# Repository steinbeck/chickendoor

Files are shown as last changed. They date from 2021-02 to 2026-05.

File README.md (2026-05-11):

# IoT Chicken Door

## Warning
This repo is here for documentation purposes only. I have retired this Chicken Door control in early 2026 and moved to a Shelly shutter control with a Shelly Plus 2PM and some relays. The software in this repo worked for many years, but was unreliable. I guess I put too much in it (lux sensor, temp, many timers). The Shelly solution is so much more reliable. :)

## Introduction
This is code for an ESP32-based Internet-of-Things (IoT) chicken door. We have a [Heini Koop chicken coop](https://www.heinicoop.de/produkt/heinicoop-huehnerstall-uno/), but the principle of this door mechanism is generic and should work with sliding and other doors.

Heini Koop Uno 
(c) Heini Koop. Picture from [Heini Koop Website](https://www.heinicoop.de/produkt/heinicoop-huehnerstall-uno/)

The ESP is hooked up to a BME280 climate sensor (not needed, just for fun) as well as a BH1750 light sensor, as well as a DC motordriver connected to a 30 cm DC actuator to open and close the door. We currently have a [ChickenGuard(TM)](https://www.chickenguard.de/) module to close and open the door. It works well, but lacks the Internet access. If you do not need the IoT functionality and do not want to tinker, go for the ChickenGuard(TM).
If, say, you are away from home and decide that you want to let the chicken out manually tomorrow, but the door is in lux-mode (opens when a certain amount of daylight is reached) then you need to live with the situation. 
Furthermore, if you discover on your coop camera :) that one of the chicken didn't get in before the door closed automatically in the evening and you are not at home, you cannot open the door remotely to let the late-comer in. In our rural area, the likelihood is high that you then have one saturated predator more in the area and one chicken less. 
Last but not least, the standard ChickenGuard (TM) door can be simply pushed up once closed. They do have a model that locks, though, but we have the standard model. The DC actuator keeps the door closed once it is closed. No way to push it up. The downside of the actuator is that it is very powerful. If something gets in the way when the door closes, it or the door gets damaged. 

Ok, so much for the motivation for this project. Here are the specs:

## Specifications

* 3 modes (manual-, time-based, light-based operation), independently selectable for opening and closing (e.g. open every morning at 8am, but close at night when the light is low).
* This obviously requires a light sensor. This one has a BH1750. You can also set a delay. If the light has been below or above threshold for a certain number of minutes, the door moves. 
* BME280 for temperature, humidity and pressure
* Manual opening and closing with two buttons at the device. 
* A INA219 current sensor that notices when the built-in end stops of the actuator have switched the device off, so the system knows when the door is fully open or closed. 
* Web interface for the settings and sensor readings.
* Linear actuator with 30 cm range of operation, IP66 approved for outdoor application. 

## Software
More todo here

Turns out that the ESP32 dev module can be picky with regard to which pins you can use for what. I tried around a bit and the following pins work for me:

* SDA 16
* SCL 17
* Motor_Pin_1 18
* Motor_Pin_2 19
* Button_1 26
* Button_2 27

## Web interface
I decided to build this device without a display and without the possiblity to adjust the settings directly at the device, apart from the two buttons to open and close the door. 
Instead, I added a web interface with a dashboard with two virtual buttons to open and close the door as well as some status information and sensor readings. 

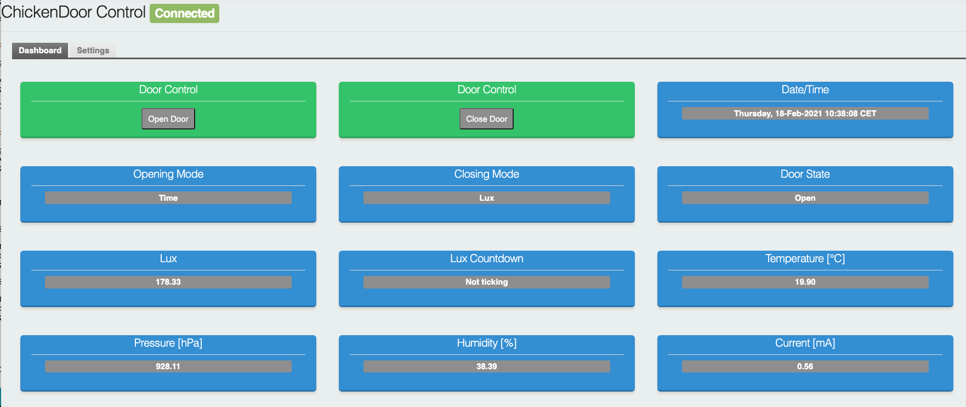
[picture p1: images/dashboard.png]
dashboard


And there is a settings panel. 

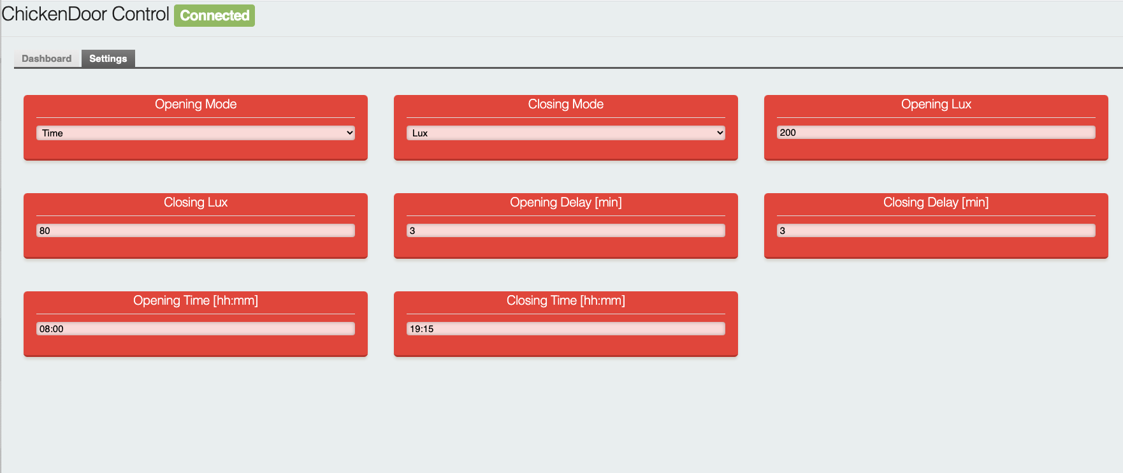
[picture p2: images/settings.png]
settings


## Development

The mechanism was first setup on a piece of plywood so I could carry it around and test and develop wherever I wanted:

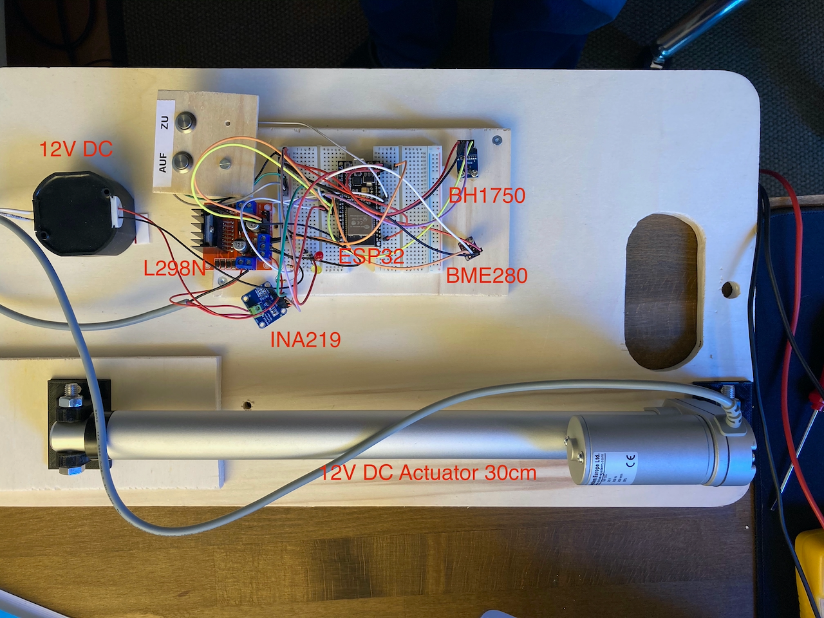
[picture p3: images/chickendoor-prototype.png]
Breadboard prototype of chicken door mechanism


Here is the fritzing schema (yes, I am sure this can be done nicer :)):

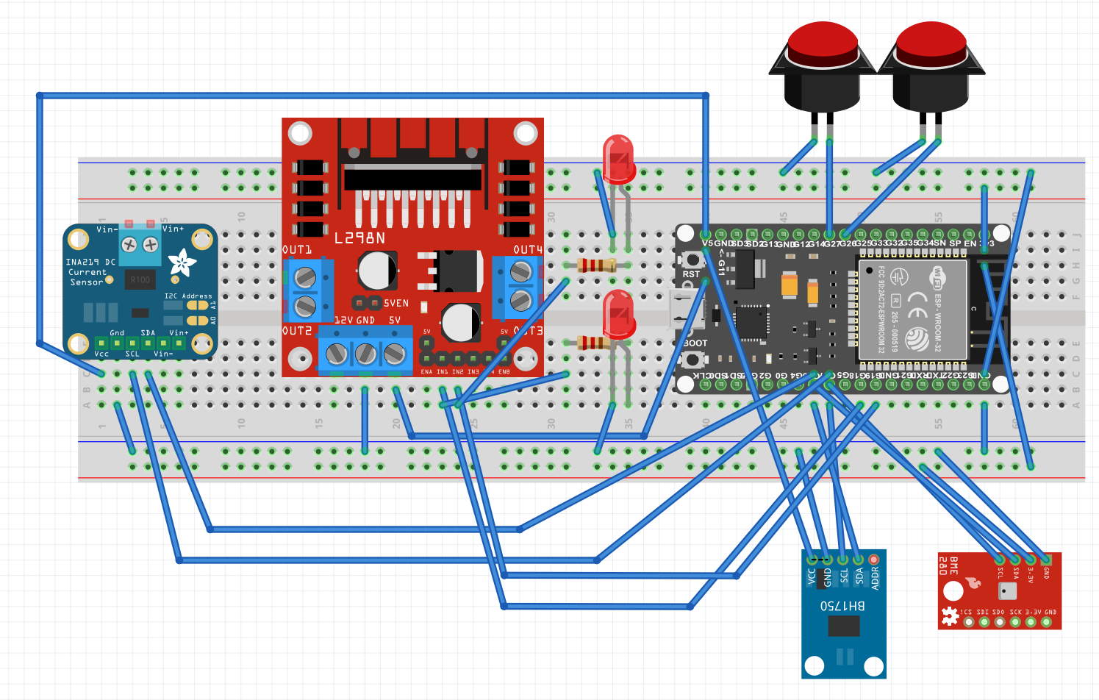
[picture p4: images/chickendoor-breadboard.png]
Breadboard prototype of chicken door mechanism


The mounts that came with the actuator where useless as too short to mount the actuator for vertical operation, so I designed a [mount in OpenSCAD](https://github.com/steinbeck/chickendoor/blob/main/actuator_mount.scad) and 3D printed it on my ender3. I eventually ordered the part in PA2020 (Nylon), 3D printed with Selective Laser Sintering (SLS), from [RapidObject GMBH](https://www.rapidobject.com/) in Germany for maximum strength and durability.

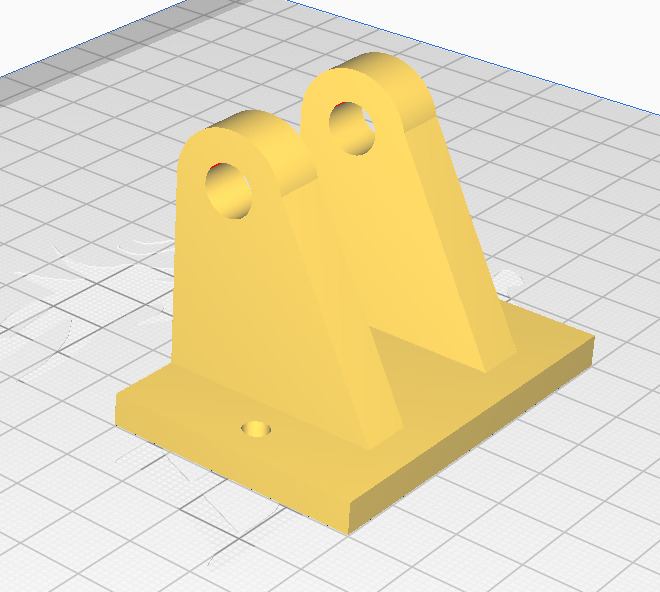
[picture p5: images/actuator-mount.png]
3D model of actuator mount


And here is the final assembly working and in action:

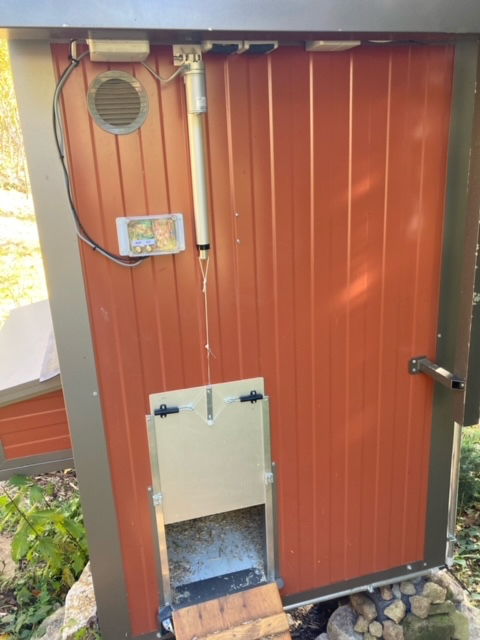
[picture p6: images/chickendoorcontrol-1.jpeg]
The whole assembly in action

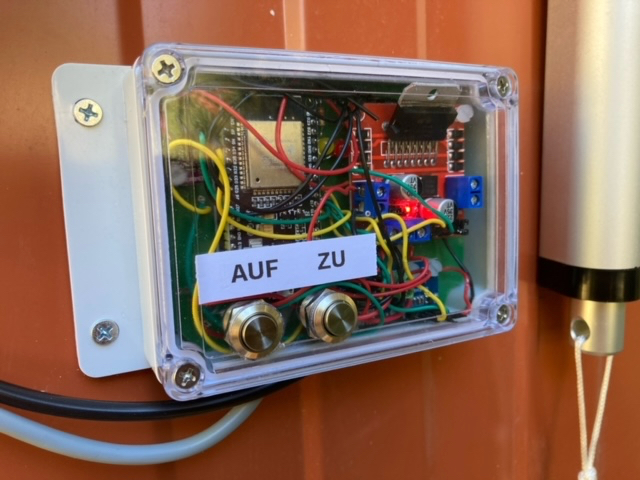
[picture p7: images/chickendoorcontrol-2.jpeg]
Close-up of control


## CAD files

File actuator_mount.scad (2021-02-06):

extrusion_length = 35;
hole_distance = 25;  // the distance of the mounting hole to the wall

mounting_plate_thickness = 5;
mounting_plate_height = 40;
mounting_plate_width = 60;
wall_screw_radius = 2;
m_screw_radius = 4; // The radius of the mounting hole in the actuator
extrusion_width = 5;
gap_width= 20;
wall_thickness = 5;
mount_wall_thickness = 8;
extrusion_height = (m_screw_radius + wall_thickness)*2;
extrusion_translation = mounting_plate_width /2 - gap_width / 2 - wall_thickness;

    union(){
        translate([0,mounting_plate_height - extrusion_height,extrusion_translation])
        {
            extrusion();
        }
        translate([0,mounting_plate_height - extrusion_height, mounting_plate_width - extrusion_translation - mount_wall_thickness])
        {
            extrusion();
        }

        mounting_plate();
    }
/*
* The part that extrudes from the mounting plate and 
*
*/
module extrusion()
{
       difference(){
            
            union()
            {    
                cube([extrusion_length, (m_screw_radius + mount_wall_thickness)*2, extrusion_width]);    
                translate([extrusion_length,extrusion_height/2,extrusion_width/2])
                {
                    cylinder(extrusion_width, m_screw_radius + wall_thickness, m_screw_radius + wall_thickness, true, $fn=1000);
                }
            }
            translate([extrusion_length, extrusion_height/2, extrusion_width/2 - 1])
            {
                cylinder(extrusion_width * 2, m_screw_radius, m_screw_radius, true, $fn=1000);
            }
        }
        translate([0, -extrusion_height - wall_thickness + 4, extrusion_width])
        {
            rotate([0,90,0])
            {
                prism(extrusion_width, mounting_plate_height - extrusion_height - 2, extrusion_length * 1.1);
            }
        }

}

module mounting_plate()
{
  
difference()
  {  
    cube([mounting_plate_thickness, mounting_plate_height, mounting_plate_width]);  
  
    translate([1, mounting_plate_height/2, mounting_plate_width*.15])
    {
            rotate([0,90,0])
            {
                wall_screw_hole();
            }
     }

    translate([1, mounting_plate_height/2, mounting_plate_width*.85])
    {
            rotate([0,90,0])
            {
                wall_screw_hole();
            }
     }
 }
}


module wall_screw_hole()
{
            cylinder(mounting_plate_thickness * 2 ,wall_screw_radius, wall_screw_radius, true, $fn=1000);
}

module prism(l, w, h){
   polyhedron(
           points=[[0,0,0], [l,0,0], [l,w,0], [0,w,0], [0,w,h], [l,w,h]],
           faces=[[0,1,2,3],[5,4,3,2],[0,4,5,1],[0,3,4],[5,2,1]]
           );
   
}

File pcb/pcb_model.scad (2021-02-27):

pcb_width = 107;
pcb_height = 77;
pcb_thickness = 1;
edge_cutout_radius = 6;
mount_hole_radius = 1.5;
mount_hole_distance_x = 78;
mount_hole_distance_y = 51;
bh1750_mount_hole_distance = 8.7;
bh1750_height = 20;
ina219_mount_hole_distance_x = 20;
ina219_mount_hole_distance_y = 17;
motor_driver_mount_hole_distance = 37;

projection() pcb();

module pcb()
{
    difference()
    {
        cube([pcb_width, pcb_height, pcb_thickness]);  
        translate([0,0,-.5])
        {
            edge_cutout();
        }
        translate([0,pcb_height,-.5])
        {
            edge_cutout();
        }
        translate([pcb_width,0,-.5])
        {
            edge_cutout();
        }
        translate([pcb_width,pcb_height,-.5])
        {
            edge_cutout();
        }

        // The four holes to mount the PCB to the case
        translate([(pcb_width - mount_hole_distance_x)/2, (pcb_height - mount_hole_distance_y)/2,-.5])
        {
            mount_hole();
        }
        translate([pcb_width-(pcb_width - mount_hole_distance_x)/2, (pcb_height - mount_hole_distance_y)/2,-.5])
        {
            mount_hole();
        }
        translate([(pcb_width - mount_hole_distance_x)/2, pcb_height - (pcb_height - mount_hole_distance_y)/2,-.5])
        {
            mount_hole();
        }
        translate([pcb_width-(pcb_width - mount_hole_distance_x)/2, pcb_height - (pcb_height - mount_hole_distance_y)/2,-.5])
        {
            mount_hole();
        }    
        
        // The two mount holes for the BH1750 light sensor
        
        translate([(pcb_width - mount_hole_distance_x)/2 - bh1750_mount_hole_distance, (pcb_height - mount_hole_distance_y)/2 +  10,-.5])
        {
            mount_hole();
        }
        translate([(pcb_width - mount_hole_distance_x)/2, (pcb_height - mount_hole_distance_y)/2 + 10,-.5])
        {
            mount_hole();
        }
        
        // The single mount hole for the BME208
        translate([(pcb_width - mount_hole_distance_x)/2 - bh1750_mount_hole_distance, (pcb_height - mount_hole_distance_y)/2 +  10 + bh1750_height + 5,-.5])
        {
            mount_hole();
        }
        
        // Four holes for the INA219 Current Sensor
        translate([pcb_width/2 + 5, 3,-.5])
        {
            mount_hole();
        }
        translate([pcb_width/2 + 5 + ina219_mount_hole_distance_x, 3,-.5])
        {
            mount_hole();
        }
        translate([pcb_width/2 + 5, 3 + ina219_mount_hole_distance_y,-.5])
        {
            mount_hole();
        }
        translate([pcb_width/2 + 5 + ina219_mount_hole_distance_x, 3 + ina219_mount_hole_distance_y,-.5])
        {
            mount_hole();
        }

        // three holes for the motor driver
        translate([pcb_width-(pcb_width - mount_hole_distance_x)/2 - motor_driver_mount_hole_distance, pcb_height - (pcb_height - mount_hole_distance_y)/2,-.5])
        {
            mount_hole();
        }    
        translate([pcb_width-(pcb_width - mount_hole_distance_x)/2 - motor_driver_mount_hole_distance, pcb_height - (pcb_height - mount_hole_distance_y)/2 - motor_driver_mount_hole_distance,-.5])
        {
            mount_hole();
        }    

        translate([pcb_width-(pcb_width - mount_hole_distance_x)/2, pcb_height - (pcb_height - mount_hole_distance_y)/2 - motor_driver_mount_hole_distance,-.5])
        {
            mount_hole();
        }    

        
    }
}

module edge_cutout()
{
    cylinder(pcb_thickness + 1, edge_cutout_radius,  edge_cutout_radius, $fn=1000);   
}

module mount_hole()
{
    cylinder(pcb_thickness + 1, mount_hole_radius, mount_hole_radius, $fn=1000);
}

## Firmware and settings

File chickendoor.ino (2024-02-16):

#include <Wire.h>
#include <BH1750.h>
#include <BME280I2C.h>
#include <WiFi.h>
#include <ezTime.h>
#include <Ticker.h>
#include <Preferences.h>
#include <Adafruit_INA219.h>

#include <AsyncEventSource.h>
#include <AsyncJson.h>
#include <SPIFFSEditor.h>
#include <WebHandlerImpl.h>
#include <ESPAsyncWebServer.h>
#include <AsyncElegantOTA.h>
#include <WebAuthentication.h>
#include <AsyncWebSynchronization.h>
#include <AsyncWebSocket.h>
#include <WebResponseImpl.h>
#include <StringArray.h>

#include <AsyncTCP.h>

#include <DNSServer.h>
#include <ESPUI.h>
#include <Update.h>
#include <PubSubClient.h>
#include <esp_task_wdt.h>
// logging to google sheets
#include <ESP_Google_Sheet_Client.h>

// MQTT library for home assistant
#include <ArduinoHA.h>


//10 seconds WDT ; Less screws up OTA
#define WDT_TIMEOUT 10
#define WL_MAC_ADDR_LENGTH 6


const byte DNS_PORT = 53;
IPAddress apIP(192, 168, 1, 1);
DNSServer dnsServer;

#if defined(ESP32)
#include <WiFi.h>
#else
#include <ESP8266WiFi.h>
#endif

//OTA with ESPUI solution thanks to user ENWI (https://githubmemory.com/repo/s00500/ESPUI/issues/116)
const char* OTA_INDEX PROGMEM
  = R"=====(<!DOCTYPE html><html><head><meta charset=utf-8><title>OTA</title></head><body><div class="upload"><form method="POST" action="/ota" enctype="multipart/form-data"><input type="file" name="data" /><input type="submit" name="upload" value="Upload" title="Upload Files"></form></div></body></html>)=====";

#include "secrets.h"

#define DOOR_UNDEFINED 0
#define DOOR_OPEN 1
#define DOOR_CLOSED 2
#define OP_MODE_MANUAL 0
#define OP_MODE_LUX 1
#define OP_MODE_TIME 2

Adafruit_INA219 ina219;
const char ssid[] = WIFI_SSID;
const char password[] = WIFI_PASSWD;
const char titleVersion[] = "Chicken Door Control V1.3.0";

WiFiClient client;
HADevice hadevice;
HAMqtt mqtt(client, hadevice);
//HASensor chickendoor("chickendoor");
HACover chickendoor("chickendoor", HACover::DefaultFeatures);

HASensorNumber volierelux("volierelux", HASensorNumber::PrecisionP1);
HASensor hadoorstate("doorstate");


// Service Account's private key
const char PRIVATE_KEY[] PROGMEM = PRIVATE_KEY_DEF;

// The ID of the spreadsheet where you'll publish the data
const char spreadsheetId[] = SPREADSHEET_ID;


// Token Callback function
void tokenStatusCallback(TokenInfo info);

//End of google sheet api config


Timezone myTZ;
BH1750 lightMeter;
BME280I2C bme;
unsigned int doorState = DOOR_UNDEFINED; // 1 is open, 2 is closed, use the defines above.
int motorPinForward = 18;
int motorPinBackward = 19;
int motorRunningSeconds = 0;
int motorRunDuration = 60;
boolean motorRunning = false;
int doorCylclingState = 0;
int networkUnreachableCount = 0;

int motorNumberPin;
int upButtonPin = 26;
int downButtonPin = 27;
// Instance of the button.
Preferences preferences;

// Web UI controls
uint16_t luxLabelId;
uint16_t luxCountdownLabelId;
uint16_t temperatureLabelId;
uint16_t pressureLabelId;
uint16_t humidityLabelId;
uint16_t currentLabelId;
uint16_t doorStateLabelId;
uint16_t logfileLabelId;

uint16_t openOperationModeSelectorId;
uint16_t closeOperationModeSelectorId;
uint16_t openOperationModeLabelId;
uint16_t closeOperationModeLabelId;
uint16_t dateTimeLabelId;
uint16_t openButtonId;
uint16_t closeButtonId;
uint16_t restartButtonId;

uint16_t closingLuxTextId;
uint16_t openingLuxTextId;
uint16_t closingLuxDelayTextId;
uint16_t openingLuxDelayTextId;
uint16_t closingTimeTextId;
uint16_t openingTimeTextId;


boolean luxTickerRunning = false;


char* modeStrings[] = {"Manual", "Lux", "Time"};

// Measurement Values
float lux;
float temperature;
float pressure;
float humidity;
/*
   If the light stays below closingLux for closingLuxdelay seconds, the door closes.
   If the light is above openingLux for openingLuxdelay seconds, the door opens.
*/
float closingLux = 300; // if light is smaller than closingLux for closingLuxDelay in minutes, then close the door
float openingLux = 500; // if light is more than openingLux for openingLuxDelay in minutes, then open the door

int closingLuxDelay;
int openingLuxDelay;

long closingLuxSeconds;
long openingLuxSeconds;
long tempClosingLuxSeconds;
long tempOpeningLuxSeconds;



char openingTime[10] = "08:00";
char closingTime[10] = "19:00";
int openingHour = 8;
int openingMinute = 0;
int closingHour = 19;
int closingMinute = 0;

unsigned int openOperationMode = OP_MODE_MANUAL;
unsigned int closeOperationMode = OP_MODE_MANUAL;

static long oldTime = 0;


double current = 0.0;

double zeroCurrent = 0.0;
int runs = 0;
int last = millis();


void checkclosingLuxDuration();
void checkopeningLuxDuration();
void checkMotorRunning();
float readLux();
void checkLux();
void checkButtons();

Ticker closingLuxTicker;
Ticker openingLuxTicker;
Ticker readCurrentTicker;
Ticker readLuxTicker;
Ticker checkLuxTicker;
Ticker buttonTicker;
Ticker startMotorTicker;
Ticker motorRunningSecondsCounter;
Ticker networkAliveTicker;
Ticker restartTicker;

long lastReconnectAttempt; // for mqttclient update in the loop function


void setup() {
  String message;
  Wire.begin(16, 17);
  delay(500);
  // sets the two motor pins (open, close) as outputs:
  GSheet.printf("ESP Google Sheet Client v%s\n\n", ESP_GOOGLE_SHEET_CLIENT_VERSION);

  pinMode(motorPinForward, OUTPUT);
  pinMode(motorPinBackward, OUTPUT);
  Serial.begin(115200);
  WiFi.setHostname("ChickenDoor");
  WiFi.setAutoReconnect(true);
  WiFi.begin(ssid, password);

  if (! ina219.begin()) {
    Serial.println("Failed to find INA219 chip");
    while (1) {
      delay(10);
    }
  }

  while ( WiFi.status() != WL_CONNECTED ) {
    delay ( 500 );
    Serial.print ( "." );
  }
  waitForSync();
  Serial.print("Wifi connected with IP ");
  Serial.println(WiFi.localIP());


  // Set the callback for Google API access token generation status (for debug only)
  GSheet.setTokenCallback(tokenStatusCallback);

  // Set the seconds to refresh the auth token before expire (60 to 3540, default is 300 seconds)
  GSheet.setPrerefreshSeconds(10 * 60);

  // Begin the access token generation for Google API authentication
  GSheet.begin(CLIENT_EMAIL, PROJECT_ID, PRIVATE_KEY);


  writelog("Chicken Door Control (re)started");
  writelog(String(WiFi.localIP().toString().c_str()));
  writelog(WiFi.SSID());
  writelog(String(WiFi.RSSI()));

  myTZ.setLocation(F("Europe/Berlin"));
  loadPreferences();
  message = "Network unreachable count: ";
  message.concat(networkUnreachableCount);
  writelog(message);

  setupWebUI();
  setupMQTT();
  pinMode(upButtonPin, INPUT_PULLDOWN);
  pinMode(downButtonPin, INPUT_PULLDOWN);
  lightMeter.begin();
  bme.begin();
  networkUnreachableCount = 0;

  networkAliveTicker.attach(20, checkNetworkAlive);
  for (int i = 0; i < 10; i++) readLux();
  esp_task_wdt_init(WDT_TIMEOUT, true); //enable panic so ESP32 restarts
  esp_task_wdt_add(NULL); //add current thread to WDT watch
  lastReconnectAttempt = 0;

}

//************************
//This is the central loop
//************************

void loop() {
  checkButtons();
  checkMotorRunning();
  updateWebUI();
  if (openOperationMode == OP_MODE_LUX || closeOperationMode == OP_MODE_LUX)
  {
    checkLux();
  }
  if (openOperationMode == OP_MODE_TIME || closeOperationMode == OP_MODE_TIME)
  {
    checkTime();
  }

  if (millis() - last >= 8000) {
    esp_task_wdt_reset();
    last = millis();
  }
  mqtt.loop();
  delay(200);
}

void checkButtons()
{
  int upButtonState = digitalRead(upButtonPin);
  int downButtonState = digitalRead(downButtonPin);

  //  Serial.print("upButtonPin: "); //  Serial.println(upButtonState); //  Serial.print("downButtonPin: "); //  Serial.println(downButtonState); //  if (downButtonState == 1 && doorState == DOOR_OPEN) closeDoor(); //  else if (upButtonState == 1 && doorState == DOOR_CLOSED) openDoor();

  if (downButtonState == 1)
  {
    writelog("The down button was pressed manually");
    closeDoor();
  }
  else if (upButtonState == 1)
  {
    writelog("The up button was pressed manually");
    openDoor();
  }
}

void checkLux()
{
  if (luxTickerRunning)
  {
    //Serial.println("Lux Ticker is already running");
    return;
  }
  if (closeOperationMode == OP_MODE_LUX && lux < closingLux && doorState == DOOR_OPEN)
  {
    String message = "Door closing in " + String(closingLuxDelay - (closingLuxSeconds / 60)) + " minutes";
    writelog(message);
    ESPUI.print(luxCountdownLabelId, message);
    closingLuxSeconds = 0;
    tempClosingLuxSeconds = 0;
    luxTickerRunning = true;
    closingLuxTicker.attach(1, checkClosingLuxDuration);
    return;
  }
  if (openOperationMode == OP_MODE_LUX && lux > openingLux && doorState == DOOR_CLOSED)
  {
    String message = "Door opening in " + String(openingLuxDelay - (openingLuxSeconds / 60)) + " minutes";
    ESPUI.print(luxCountdownLabelId, message);
    writelog(message);
    openingLuxSeconds = 0;
    tempOpeningLuxSeconds = 0;
    luxTickerRunning = true;
    openingLuxTicker.attach(1, checkOpeningLuxDuration);
    return;
  }
}


void setupWebUI()
{
  uint16_t dashboardTab = ESPUI.addControl( ControlType::Tab, "Dashboard", "Dashboard" );
  uint16_t settingsTab = ESPUI.addControl( ControlType::Tab, "Settings", "Settings" );
  openOperationModeSelectorId = ESPUI.addControl( ControlType::Select, "Opening Mode", modeStrings[openOperationMode], ControlColor::Alizarin, settingsTab, &operationModeSelector );
  ESPUI.addControl( ControlType::Option, modeStrings[0], modeStrings[0], ControlColor::Alizarin, openOperationModeSelectorId );
  ESPUI.addControl( ControlType::Option, modeStrings[1], modeStrings[1], ControlColor::Alizarin, openOperationModeSelectorId);
  ESPUI.addControl( ControlType::Option, modeStrings[2], modeStrings[2], ControlColor::Alizarin, openOperationModeSelectorId );
  closeOperationModeSelectorId = ESPUI.addControl( ControlType::Select, "Closing Mode", modeStrings[closeOperationMode], ControlColor::Alizarin, settingsTab, &operationModeSelector );
  ESPUI.addControl( ControlType::Option, modeStrings[0], modeStrings[0], ControlColor::Alizarin, closeOperationModeSelectorId );
  ESPUI.addControl( ControlType::Option, modeStrings[1], modeStrings[1], ControlColor::Alizarin, closeOperationModeSelectorId);
  ESPUI.addControl( ControlType::Option, modeStrings[2], modeStrings[2], ControlColor::Alizarin, closeOperationModeSelectorId );

  openingLuxTextId = ESPUI.addControl( ControlType::Text, "Opening Lux", String(openingLux), ControlColor::Alizarin, settingsTab, &textHandler);
  closingLuxTextId = ESPUI.addControl( ControlType::Text, "Closing Lux", String(closingLux), ControlColor::Alizarin, settingsTab, &textHandler);
  openingLuxDelayTextId = ESPUI.addControl( ControlType::Text, "Opening Delay [min]", String(openingLuxDelay), ControlColor::Alizarin, settingsTab, &textHandler);
  closingLuxDelayTextId = ESPUI.addControl( ControlType::Text, "Closing Delay [min]", String(closingLuxDelay), ControlColor::Alizarin, settingsTab, &textHandler);


  snprintf(openingTime, sizeof(openingTime), "%02i:%02i", openingHour, openingMinute);
  snprintf(closingTime, sizeof(closingTime), "%02i:%02i", closingHour, closingMinute);

  openingTimeTextId = ESPUI.addControl( ControlType::Text, "Opening Time [hh:mm]", String(openingTime), ControlColor::Alizarin, settingsTab, &textHandler);
  closingTimeTextId = ESPUI.addControl( ControlType::Text, "Closing Time [hh:mm]", String(closingTime), ControlColor::Alizarin, settingsTab, &textHandler);

  openButtonId = ESPUI.addControl( ControlType::Button, "Door Control", "Open Door", ControlColor::Emerald, dashboardTab, &buttonHandler);
  closeButtonId = ESPUI.addControl( ControlType::Button, "Door Control", "Close Door", ControlColor::Emerald, dashboardTab, &buttonHandler);

  dateTimeLabelId = ESPUI.addControl( ControlType::Label, "Date/Time", "", ControlColor::Peterriver, dashboardTab);

  luxLabelId = ESPUI.addControl( ControlType::Label, "Lux", "lux", ControlColor::Peterriver, dashboardTab);
  luxCountdownLabelId = ESPUI.addControl( ControlType::Label, "Lux Countdown", "Not ticking", ControlColor::Peterriver, dashboardTab);
  doorStateLabelId = ESPUI.addControl( ControlType::Label, "Door State", "", ControlColor::Peterriver, dashboardTab);
  temperatureLabelId = ESPUI.addControl( ControlType::Label, "Temperature [°C]", "", ControlColor::Peterriver, dashboardTab);
  pressureLabelId = ESPUI.addControl( ControlType::Label, "Pressure [hPa]", "", ControlColor::Peterriver, dashboardTab);
  humidityLabelId = ESPUI.addControl( ControlType::Label, "Humidity [%]", "", ControlColor::Peterriver, dashboardTab);
  currentLabelId = ESPUI.addControl( ControlType::Label, "Current [mA]", "", ControlColor::Peterriver, dashboardTab);
  openOperationModeLabelId = ESPUI.addControl( ControlType::Label, "Opening Mode", "", ControlColor::Peterriver, dashboardTab);
  closeOperationModeLabelId = ESPUI.addControl( ControlType::Label, "Closing Mode", "", ControlColor::Peterriver, dashboardTab);

  restartButtonId = ESPUI.addControl( ControlType::Button, "Chicken Door Control Device", "Restart Device", ControlColor::Alizarin, dashboardTab, &buttonHandler);


  //logfileLabelId = ESPUI.addControl( ControlType::Label, "logfile", "", ControlColor::Peterriver,dashboardTab);


  ESPUI.begin(titleVersion);
  ESPUI.server->on("/ota",
                   HTTP_POST,
  [](AsyncWebServerRequest * request) {
    request->send(200);
  },
  handleOTAUpload);

  ESPUI.server->on("/ota",
                   HTTP_GET,
  [](AsyncWebServerRequest * request) {
    AsyncWebServerResponse* response = request->beginResponse_P(200, "text/html", OTA_INDEX);
    request->send(response);
  }
                  );

}

void updateWebUI()
{
  String message;
  if (luxTickerRunning == false) ESPUI.print(luxCountdownLabelId, "Not ticking");
  if (millis() - oldTime > 5000) {
    readLux();
    readClimateData();
    readCurrent();
    reportMQTT();
    ESPUI.print(dateTimeLabelId, String(myTZ.dateTime()));
    ESPUI.print(luxLabelId, String(readLux()));
    ESPUI.print(temperatureLabelId, String(temperature));
    ESPUI.print(pressureLabelId, String(pressure / 100));
    ESPUI.print(humidityLabelId, String(humidity));
    ESPUI.print(currentLabelId, String(readCurrent()));
    switch (doorState)
    {
      case DOOR_OPEN:
        ESPUI.print(doorStateLabelId, "Open");
        break;
      case DOOR_CLOSED:
        ESPUI.print(doorStateLabelId, "Closed");
        break;
      case DOOR_UNDEFINED:
        ESPUI.print(doorStateLabelId, "Undefined");
        break;

    }

    switch (openOperationMode)
    {
      case OP_MODE_MANUAL:
        ESPUI.print(openOperationModeLabelId, modeStrings[0]);
        break;
      case OP_MODE_LUX:
        message = modeStrings[1];
        message += " > "; message += openingLux; message += ", delay "; message += openingLuxDelay; message += " min";
        ESPUI.print(openOperationModeLabelId, message);
        break;
      case OP_MODE_TIME:
        message = modeStrings[2];
        message += " "; message += openingTime;
        ESPUI.print(openOperationModeLabelId, message);
        break;
    }

    switch (closeOperationMode)
    {
      case OP_MODE_MANUAL:
        ESPUI.print(closeOperationModeLabelId, modeStrings[0]);
        break;
      case OP_MODE_LUX:
        message = modeStrings[1];
        message += " < "; message += closingLux; message += ", delay "; message += closingLuxDelay; message += " min";
        ESPUI.print(closeOperationModeLabelId, message);
        break;
      case OP_MODE_TIME:
        message = modeStrings[2];
        message += " ";  message += closingTime;
        ESPUI.print(closeOperationModeLabelId, message);
        break;
    }
    oldTime = millis();
  }
}

void loadPreferences()
{
  //Serial.println("Reading Preferences: ");
  preferences.begin("chickendoor", false);
  unsigned int tempDoorState = preferences.getUInt("doorstate", 0);
  openOperationMode = preferences.getUInt("opopmod", 0);
  //Serial.print("openOperationMode: "); Serial.println(openOperationMode);
  closeOperationMode = preferences.getUInt("clopmod", 0);
  //Serial.print("closeOperationMode: "); Serial.println(closeOperationMode);
  closingLux = preferences.getFloat("cllux");
  openingLux = preferences.getFloat("oplux");
  closingLuxDelay = preferences.getFloat("clluxdel");
  openingLuxDelay = preferences.getFloat("opluxdel");
  openingHour = preferences.getUInt("optimehh");
  openingMinute = preferences.getUInt("optimemm");
  closingHour = preferences.getUInt("cltimehh");
  closingMinute = preferences.getUInt("cltimemm");
  networkUnreachableCount = preferences.getUInt("netuc");

  preferences.end();

  // postprocessing of preferences
  //if (tempDoorState == DOOR_UNDEFINED)
  //{
  //  writelog("door state undefined. Cycling door states ...");
  //  checkDoorCycled();
  //}
  //else doorState = tempDoorState;
}

void operationModeSelector(Control *sender, int type)
{
  int tempOpMode;

  if (sender->value == "Manual") tempOpMode = OP_MODE_MANUAL;
  else if (sender->value == "Lux") tempOpMode = OP_MODE_LUX;
  else if (sender->value == "Time") tempOpMode = OP_MODE_TIME;

  if (sender->id == openOperationModeSelectorId) openOperationMode = tempOpMode;
  else if (sender->id == closeOperationModeSelectorId) closeOperationMode = tempOpMode;

  preferences.begin("chickendoor", false);
  Serial.println(preferences.putUInt("opopmod", openOperationMode));
  Serial.print("Writing setting -> openOperationMode: "); Serial.println(openOperationMode);
  Serial.println(preferences.putUInt("clopmod", closeOperationMode));
  Serial.print("Writing setting -> closeOperationMode: "); Serial.println(closeOperationMode);
  preferences.end();

  if (tempOpMode == OP_MODE_MANUAL || tempOpMode == OP_MODE_TIME)
  {
    if (luxTickerRunning)
    {
      luxTickerRunning = false;
      closingLuxTicker.detach();
      openingLuxTicker.detach();
    }
  }
}

void buttonHandler(Control *sender, int type)
{
  if (type == B_UP)
  {
    Serial.println(sender->id);
    Serial.println(sender->value);

    if (sender->id == openButtonId)
    {
      writelog("The open button was pressed in the web interface");
      openDoor();
      return;
    }
    if (sender->id == closeButtonId)
    {
      writelog("The close button was pressed in the web interface");
      closeDoor();
      return;
    }
    if (sender->id == restartButtonId)
    {
      writelog("The restart button was pressed in the web interface");
      ESP.restart();
      return;
    }

  }
}

void textHandler(Control *sender, int type)
{

  String message;
  int tempInt;
  float tempFloat;
  if (sender->id == openingLuxTextId)
  {
    tempInt = sender->value.toInt();
    if (tempInt > 0)
    {
      openingLux = tempInt;
      preferences.begin("chickendoor", false);
      preferences.putFloat("oplux", openingLux);
      preferences.end();
    }
  }
  if (sender->id == closingLuxTextId)
  {
    tempInt = sender->value.toInt();
    if (tempInt > 0)
    {
      closingLux = tempInt;
      preferences.begin("chickendoor", false);
      preferences.putFloat("cllux", closingLux);
      preferences.end();
    }
  }
  if (sender->id == closingLuxDelayTextId)
  {
    tempInt = sender->value.toInt();
    if (tempInt > 0)
    {
      closingLuxDelay = tempInt;
      preferences.begin("chickendoor", false);
      preferences.putFloat("clluxdel", closingLuxDelay);
      preferences.end();
    }
  }
  if (sender->id == openingLuxDelayTextId)
  {
    tempInt = sender->value.toInt();
    if (tempInt > 0)
    {
      openingLuxDelay = tempInt;
      preferences.begin("chickendoor", false);
      preferences.putFloat("opluxdel", openingLuxDelay);
      preferences.end();
    }
  }

  if (sender->id == openingTimeTextId)
  {
    int tempHour = getHour(sender->value);
    int tempMinute = getMinute(sender->value);

    message = "Opening Time changed to ";
    message.concat(tempHour);
    message.concat(":");
    message.concat(tempMinute);
    writelog(message);


    if (tempHour > -1 && tempMinute > -1)
    {
      openingHour = tempHour;
      openingMinute = tempMinute;

      preferences.begin("chickendoor", false);
      preferences.putUInt("optimehh", openingHour);
      preferences.putUInt("optimemm", openingMinute);
      preferences.end();
    }
  }


  if (sender->id == closingTimeTextId)
  {
    int tempHour = getHour(sender->value);
    int tempMinute = getMinute(sender->value);
    if (tempHour > -1 && tempMinute > -1)
    {
      closingHour = tempHour;
      closingMinute = tempMinute;

      preferences.begin("chickendoor", false);
      preferences.putUInt("cltimehh", closingHour);
      preferences.putUInt("cltimemm", closingMinute);
      preferences.end();
    }
  }

}

int getHour(String timeString)
{
  int hourInt = -1;
  int colonIndex = timeString.indexOf(':');
  if (colonIndex > 0)
  {
    hourInt = timeString.substring(0, colonIndex).toInt();
  }
  return hourInt;
}

int getMinute(String timeString)
{
  int minuteInt = -1;
  int colonIndex = timeString.indexOf(':');
  if (colonIndex > 0)
  {
    minuteInt = timeString.substring(colonIndex + 1, timeString.length()).toInt();
  }
  return minuteInt;
}

void openDoor()
{
  writelog("call to openDoor");
  if (motorRunning == false)
  {
    moveDoor(motorPinBackward);
    doorState = DOOR_UNDEFINED;
    hadoorstate.setValue("Undefined");
    preferences.begin("chickendoor", false);
    preferences.putUInt("doorstate", doorState);
    preferences.end();
    writelog("Starting to open door ...");
    writelog("Setting door state to UNDEFINED");
  }
  else Serial.println("Motor already moving");

  luxTickerRunning = false;
  openingLuxTicker.detach();
}
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

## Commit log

2021-01-18 Working version of light sensor model
    The system now waits for a given time if the light is above or below a threshold and then opens or closes the door.
2021-01-21 Migration to ESP32
    The principle function is now working also with the ESP32 dev board to which I migrated. Still problem to use the Amperemeter.
    [chickendoor.ino]
2021-01-24 Update chickendoor.ino
    Saving state of the project before removing interupt based button handling.
2021-02-03 Added proper current detection for door
    Added proper current detection for door. With a new current detector, I can now check if the door is moving and when it has reached its end stop.
2021-02-03 Added 3D model for actuator mount
    Added 3D model for actuator mount. This is an openSCAD model, a free software for parametric modelling. I still need to migrate all the hand coded values to variable for more flexibility.
    [actuator_mount.scad]
2021-02-03 More variables in the openSCAD model
    More variables in the openSCAD model
    [actuator_mount.scad]
2021-02-04 Fully parameterized openSCAD file
    The openSCAD file for the mount is now fully parameterized with variables with maximum flexibility. Needs more documentation though.
    [actuator_mount.scad]
2021-02-06 Made the mount thicker
    Made the mount thicker, since the old one broke very easily. I guess, a professional print in Nylon will fix it all.
    [actuator_mount.scad]
2021-02-15 Create pcb_model.scad
    Added an openSCAD model for the PCB board of this IoT device
    [pcb_model.scad]
2021-02-18 Lux-based opening and closing now working
    The Lux-based opening and closing of the chicken door should now be working.
    [pcb_model.scad]
2021-02-18 Finished implementation
    This submit marks the implementation of a first, fully functional prototype :)
2021-02-18 Create chicken-door-breadboard .png
    Picture of breadboard prototype
2021-02-18 Update README.md
    Added picture of breadboard prototype
2021-02-18 Create actuator-mount.png
    Added picture of the 3D-printable model of the actuator mount
2021-02-18 Update README.md
    Added picture of actuator mount model
2021-02-18 pcbboard.svg now exported from OpenSCAD model
    pcbboard.svg now exported from OpenSCAD model
    [pcb_model.scad]
2021-02-18 Update pcb_model.scad
    Restored functional version of openSCAD pcb file from Dropbox
    [pcb_model.scad]
2021-02-27 Adding files for PCB
    Adding Fritzing file and gerber files for the Printed Circuit Board (PCB)
    [chickendoor-fritzing.fzz, pcb_model.scad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]
2021-10-24 Added photos of the final assembly in action
2022-03-13 Fixed time display
    Fixed time display
    [chickendoor.ino]
2022-03-24 Many bug fixes and more logging
    Fixed a number of bugs related to displaying ticker information
    Added more logging information
    [chickendoor.ino]
2022-08-27 Update chickendoor.ino
    Added restart button. Migrated to latest libraries, which required changing ESPUI code because it depends on littlefs which was renamed and moved into the EDP32 core libraries.
2022-09-04 Fixed door cycling in case of door state undefined
    This never actually worked and not bricked the chickendoor. Fixed for now
    [chickendoor.ino]
2024-02-16 disabled door cycling at startup
    disabled door cycling at startup when door is in undefined state. This leads to crashes when door has reached one of the two extreme points.
    [chickendoor.ino]
